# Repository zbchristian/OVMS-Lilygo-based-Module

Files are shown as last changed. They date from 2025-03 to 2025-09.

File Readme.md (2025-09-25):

Open-Vehicle-Monitoring-System: Module based on Lilygo T-Call A7670E V1.0/V1.1
==============================================================================
The Lilygo T-Call modules provide most of the hardware required for an OVMS module:
- ESP32-WROVER E with 4MB Flash and 8MB PSRAM
- Simcom A7670E 4G modem with GPS 
- Included antennas for 4G and GPS
- USB-C port for programming and powering during testing
- ext 5V powering possible via pin
- Price is around 35€ + tax

**This module supports only 2 CAN buses. This might limit the suitability for your car!**

OVMS Requirements
----------------- 
- Connection to OBD-II connector
- Powering via 12V of the OBD-II connector
- OBD-II to DSub-9 cable 

Communication with the car via CAN-bus requires
- Physical layer(s) and CAN controller
- 12V to 5V DC/DC converter and including filtering

Hardware
========
The Lilygo board is placed onto a motherboard, either into a socket, or the pins can be directly soldered to the board. The motherboard provides the voltage for the Lilygo board and the DSub-9 connector to connect to the OBD-II.
The board revision B is suitable for the T-Call version 1.0 and 1.1 (different GPIO mapping).

The image shows the module, the antennas and the 3D printed case (Freecad and Step files availybe in the `CAD` folder). The motherboard slides into slots and the lid will hold it in place.
The lid allows to store the GPS antenna, but allows to add SMA connectors for external antennas as well. The 4G antenna can be stored in a 1mm high compartment inside the case.

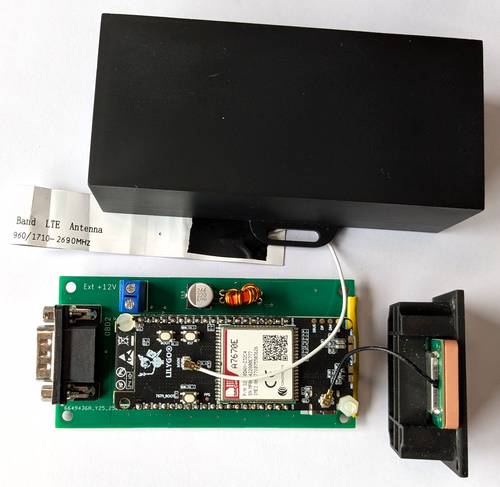
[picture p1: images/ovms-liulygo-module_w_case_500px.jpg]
OVMS module based on Lilygo T-Call


*The Lilygo based module and case. The GPS-antenna is placed into a corresponding slot in the lid of the case*

The chosen orientation (Simcom 7670 on the top) of the Lilygo board allows for easy access to the antenna connectors. The ESP32 WROVER E is in this case located on the bottom side.  

Features of the motherboard
---------------------------
The Lilygo T-Call is placed on a motherboard 
- size 49 x 98 mm²
- DSub-9 connector (pinout compatible standard OVMS module) to connect to the OBD-II
- 12V car battery input from the OBD-II, or a separate power souce 
- Fuse and filtering (common mode choke and capacitors) of the input voltage 
- DC/DC converter to provide the Lilygo board with 5V
    - Auto shutdown of the DC/DC converter at a voltage below 11.7V to prevent the drainage of the battery
    - A voltage of more than 11.9V is required to switch on again
- Two CAN busses are implemented
    - ESP32 internal requires only a physical layer
    - Second bus with an MCP2515 controller
    - Solder jumpers to enable 120 &Omega; bus termination resistors 
- Voltage divider to measure the battery voltage
- The schematic and board layout is provided for Autodesk Eagle
- The Gerber and bill of material is provided for the board production and assembly at JLCPCB 
- Nearly all components are placed on the bottom side of the PCB. This allows for an easy access, even when the Lilygo board is soldered to the motherboard
- 3D printable case to house the motherboard as well as the antennas
    - sufficient space in the lid to add SMA connectors for external antennas

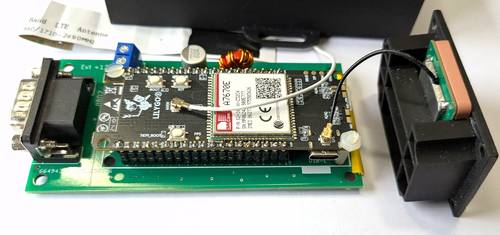
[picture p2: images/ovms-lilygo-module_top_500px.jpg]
OVMS module based on Lilygo T-Call - Top side

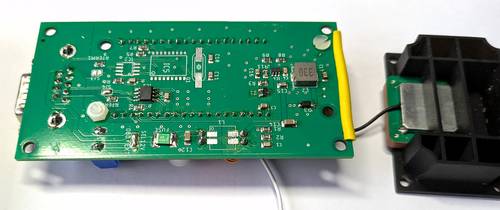
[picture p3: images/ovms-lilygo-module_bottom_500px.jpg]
OVMS module based on Lilygo T-Call - Bottom side


*Top and bottom side of the module. Only a single CAN bus is assembled, because the module is used for a car with a single bus. Therefore the second physical layer and the MCP2515 is left empty*

Limitations
-----------
- The flash memory size of only 4MB Flash does no allow Over-the-Air updates of the firmware. So, each change requires access via the USB-C port 
- Only two CAN buses
- No GPIO extender
- No SD-Card support

Assembly related hints
----------------------
The Lilygo module can in principle be soldered directly to the board by using the provided pin headers. The board has to be mounted with the Simcom modem on the top side.
Using a precision socket and corresponding pin headers, the module can easliy be removed again, but should be secured by non conducting screws.
 
The DC-DC converter output voltage is defined by R8 and R9. The reference voltage is 0.8V, so with R8=100k and R9=18k, the output voltage is about 5.2V.
The Schottky diode reduces this by about 0.4V, hence the Lilygo module is powered by 4.8V. The diode is necessary to allow to provide power via the USB-C 
port at the same time, i.e. when flashing a new firmware. 

The DC-DC converter exhibits an enable input, which requires a minimum voltage to power on of 1.2V and to power off of 1.0V. The enable voltage is derived from the 
input voltage by means of the Zener diode Z1 and the voltage divider R3/R11. For a Zener voltage of 10V, the default values R3=100k and R11=220k lead to 
a minimal power on voltage of 11.8V and a maximal power off voltage of 11.5V. In case a different Zener voltage is used, the divider has to be adjusted accordingly. 

Firmware
--------
Except for the above mentioned limitation, the module is compatible with the standard OVMS firmware, BUT the pinout requires a remapping of the ESP32 pins.
This is implemented in the [OVMS repository](https://github.com/openvehicles/Open-Vehicle-Monitoring-System-3). 
- Follow the standard OVMS documentation to clone the above repository, install the required additional packages and install the required Espressif IDF
- In the folder `./vehicle/OVMS.V3` copy `support/sdkconfig.lilygo_tc` to `sdkconfig` and `support/partition4M.csv` to `partition4M.csv`
- Run `make menuconfig` and go to `Component config -> Opene Vehicle Monitoring System (OVMS) -> Hardware support`.
  - Hardware Version should be 3.1
  - Enable GPIO remapping under `Choose GPIO Mapping`
  - Now a new menu entry appears in `Hardware support` called `File with GPIO mapping`
	- For the above `sdkconfig`, the default file is `lilygo_tc_v11.h`. This is valid for the Rev B motherboard and a Lilygo A7670E T-Call V1.1
	- The GPIO mappings files are located in the folder `components/gpio_maps`
- Be sure, that the following OVMS components are disabled: MAX7317, external SWCAN, Over-The-Air update, SD card
- Disable the support for all cars (`vehicle support`) except for the one you are interested in. This is required to meet the limited space in the Flash memory for the firmware
  - For the default `partitions4M.csv`, the available space for the firmware is `0x2f0000 = 3080192B = 2.94MB`. The full firmware requires about 3.5MB.
  - **The support for the *Nissan Leaf* and *Renault Twizzy* should always be disabled, since these do not compile without the MAX7317 support.**  
- Follow the standard documentation to compile and flash the firmware via USB
  - Check the size of the firmware: `ls -la build/ovms3.bin`
- If the flash process is failing due to a too large firmware
  - disable some additional cars under `Vehicle support`
  - if no corresponding scripts are utilized, disable the Javascript support (under `OVMS3 library suppoprt`). This saves about 220kB
  - disable components which are not needed, like the *ZIP archive support* (`OVMS3 library support`) and the `OVMS3 component options` *Reverse Engineering tools*, *ECU scanning*, *File editor*, *Plugins*
- The above limitation for the firmware size can be reduced, by using a modified partition table ([`partitions4M_full.csv`](partitions4M_full.csv)) from this repository
  - This reduces the `FAT` partition, the storage for the OVMS configuration, from `1MB` to `512kB`, which might cause problems in your setup!
  - In this case the available space for the firmware is `0x370000 = 3604480B = 3.44MB`

Alternative GPIO mapping
-------
Alternative GPIO mapping files are available and can be placed in the folder [`components/gpio_maps`](https://github.com/openvehicles/Open-Vehicle-Monitoring-System-3/tree/master/vehicle/OVMS.V3/components/gpio_maps). 

Check the [Readme](https://github.com/openvehicles/Open-Vehicle-Monitoring-System-3/tree/master/vehicle/OVMS.V3/components/gpio_maps) for details about the naming of the GPIO pins and the format of the mapping files.

Known Issues
------------
- An outdated firmware version of the Simcom A7670E can cause connection problems. The firmware can be updated according to the
[Modem Firmware Update Guide](https://github.com/Xinyuan-LilyGO/LilyGO-T-A76XX/blob/main/docs/update_fw.md). 
This requires to solder an USB cable to the corresponding pins on the Lilygo board (see [here](https://github.com/Xinyuan-LilyGO/LilyGO-T-A76XX/issues/180)).

Disclaimer
==========
This design is provided as is. Use at your own risk.

Enjoy!

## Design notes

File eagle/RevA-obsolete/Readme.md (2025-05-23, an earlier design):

Obsolete Revision A of the motherboard
======================================
The first version of the motherboard is only suitable for the Lilygo T-Call A7670E V1.0!

Due to re-arranged GPIOs is the board not compatible with T-Call V1.1.

The revision B board can be used for both T-Call versions, but requires a different GPIO mapping in the software.

Modification of a Rev A board into a Rev B: 
- Cut connection of GPIO 32 to the transceiver chip (CAN-TX) -> connect with GPIO 2
- Cut the conenction of GPIO 33 (CAN transceiver RS) -> conenct with GPIO 21

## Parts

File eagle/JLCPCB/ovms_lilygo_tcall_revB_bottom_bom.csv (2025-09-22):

Comment | Designator | Footprint | LCSC Part #
1u | C16 | C0805K
2u2 | C15 | C0805K
10K | R5 R6 R7 | M0805
10V | Z1 | SOT23
10k | R4 | M0805
18k | R9 | M0805
22pF | C10 C11 | C0805K
22u | C3 | C0805K
22u | C12 C14 | C1206K
22u | C17 | C0805K
33u | L2 | DR74
100k | R2 R3 R8 | M0805
100n | C1 C4 C6 C7 | C0805K
120 | RTERM0 RTERM1 | M0805
220k | R11 | M0805
470k | R1 | M0805
LMR51610XDBVR | IC4 | SOT23-6
MCP2515T-I/SO | IC5 | SO-18W
MF-SMDF050 | FUSE | MF-SMDF050
SS12 | D3 | SOD123
TCAN330DR | IC2 IC3 | SO-08
WE-SL2 250uH 1.2A | L1 | CHOKE_SMD
X49SM16MSD2SC | Q1 | 11.4X4.5

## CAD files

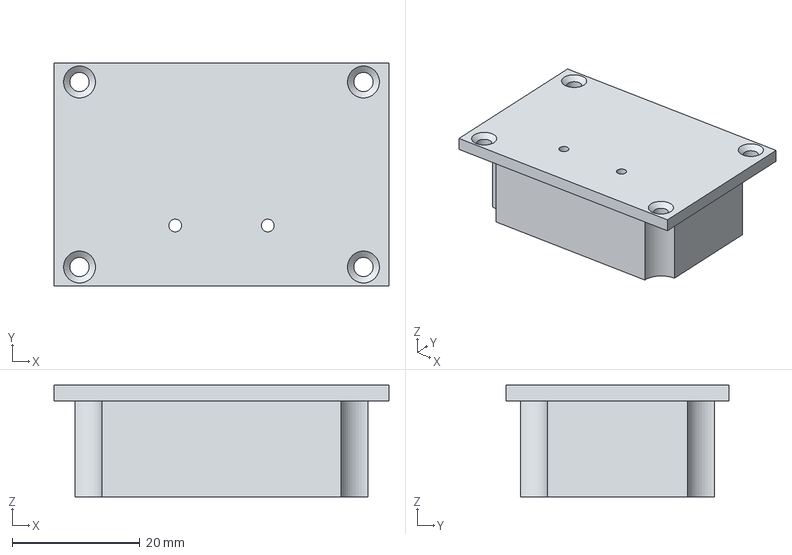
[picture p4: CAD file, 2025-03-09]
CAD/case-v2-lid.step
52.5 x 35.0 x 17.5 mm

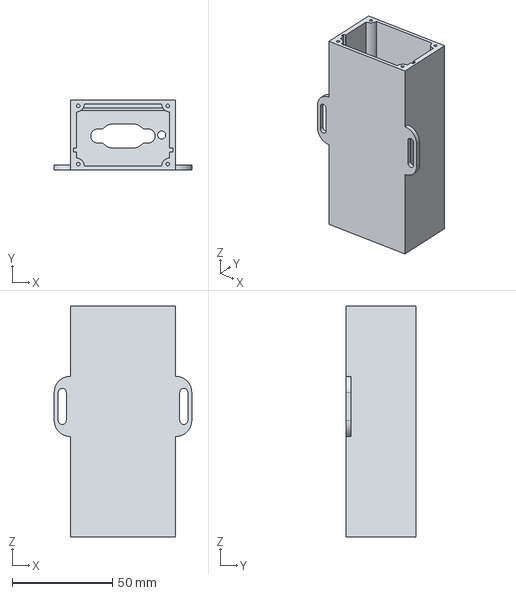
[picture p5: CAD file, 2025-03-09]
CAD/case_v2.step
68.5 x 35.0 x 115.0 mm

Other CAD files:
CAD/case-v2.FCStd

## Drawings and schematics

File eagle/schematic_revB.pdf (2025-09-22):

# GPIO22 LILYGO

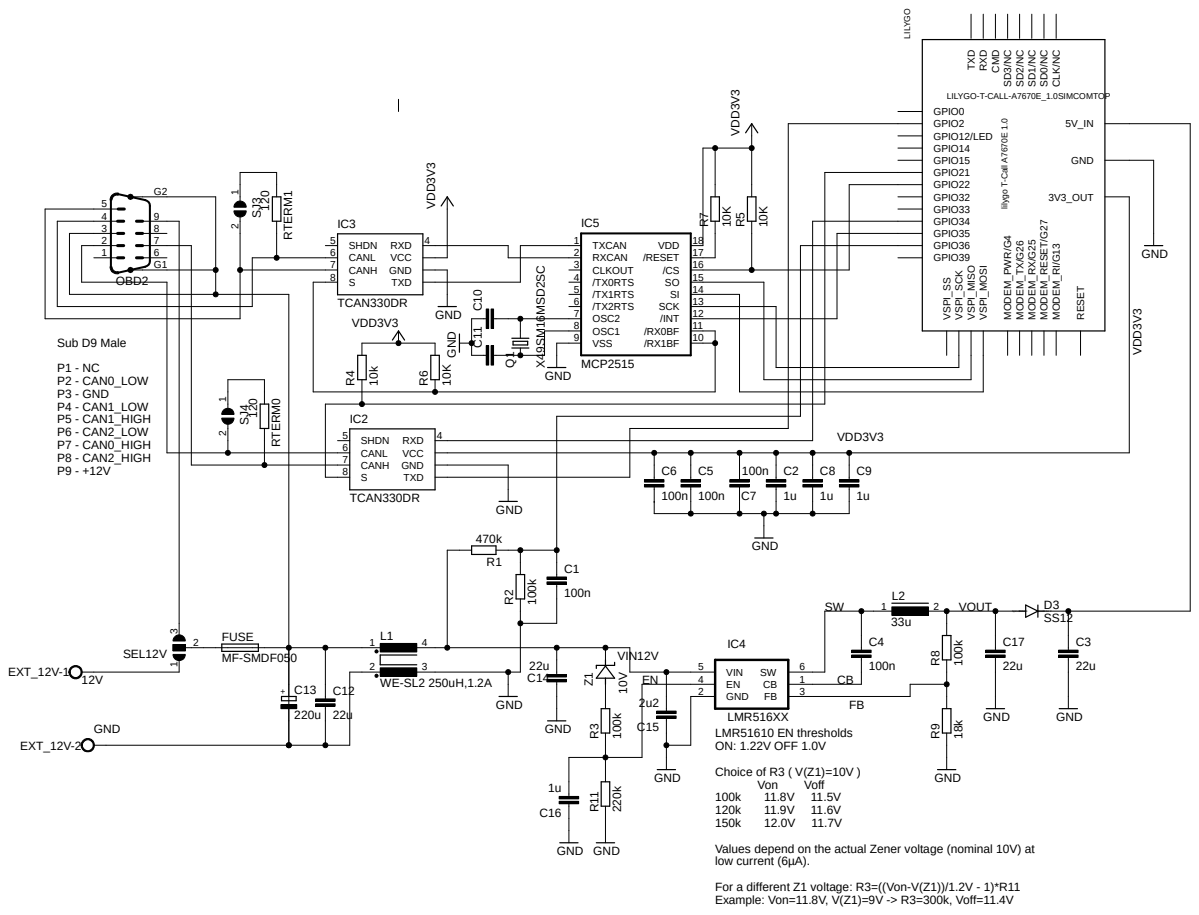
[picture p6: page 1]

3V3_OUT SD³/NC SD²/NC SD¹/NC SD⁰/NC CLK/NC TXD RXD CMD

LMR51610 EN thresholds
ON: 1.22V OFF 1.0V
Choice of R3 ( V(Z1)=10V )
Values depend on the actual Zener voltage (nominal 10V) at
low current (6µA).
For a different Z1 voltage: R3=((Von-V(Z1))/1.2V - 1)*R11
Example: Von=11.8V, V(Z1)=9V -> R3=300k, Voff=11.4V

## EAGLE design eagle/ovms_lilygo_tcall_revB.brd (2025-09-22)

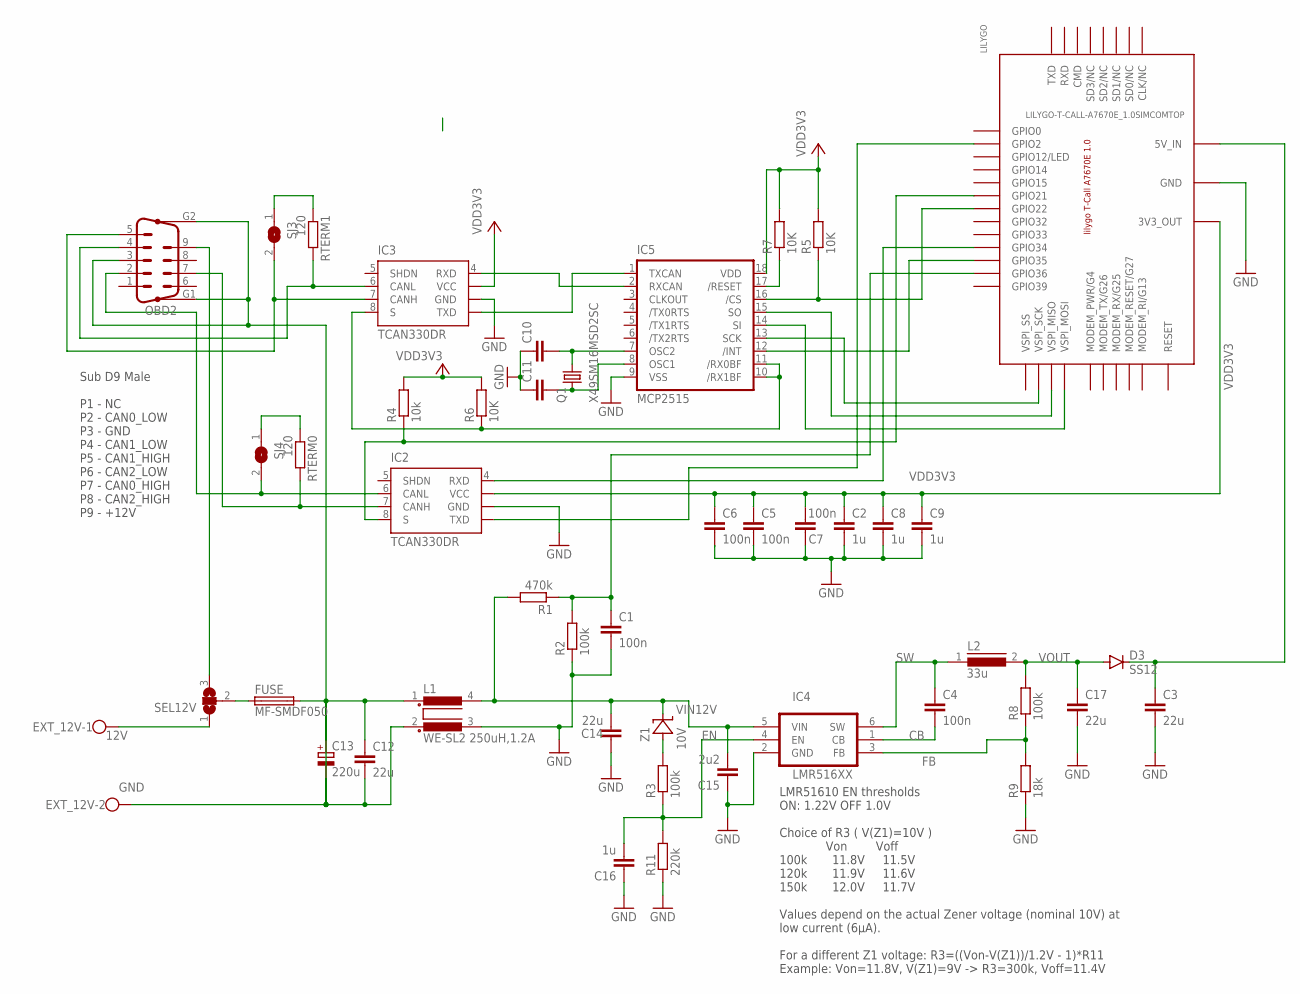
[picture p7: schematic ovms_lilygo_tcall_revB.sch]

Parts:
C1, C4, C5, C6, C7: 100n; C0805K
C2, C8, C9, C16: 1u; C0805K
C3, C17: 22u; C0805K
C10, C11: 22pF; C0805K
C12, C14: 22u; C1206K
C13: 220u; UD-8X10_NICHICON
C15: 2u2; C0805K
D3: SS12; SOD123
EXT_12V: GND; W237-102
FUSE: MF-SMDF050
IC2, IC3: TCAN330DR; SO-08
IC4: LMR516XX; SOT23-6
IC5: MCP2515; SO-18W
L1: WE-SL2 250uH,1.2A; CHOKE_SMD
L2: 33u; DR74
LILYGO: LILYGO-T-CALL-A7670E_1.0SIMCOMTOP; LILYGO-TCALL-A7670E_1.0
OBD2: M09HP
Q1: X49SM16MSD2SC; 11.4X4.5
R1: 470k; M0805
R2, R3, R8: 100k; M0805
R4: 10k; M0805
R5, R6, R7: 10K; M0805
R9: 18k; M0805
R11: 220k; M0805
RTERM0, RTERM1: 120; M0805
SEL12V: SJ2W; SJ_2
SJ3, SJ4: SJ
Z1: 10V; SOT23

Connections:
12V: C12.1, C13.+, FUSE.2, L1.1
CB: C4.2, IC4.1 (CB)
EN: C16.2, IC4.4 (EN), R3.1, R11.2
EXT12V: EXT_12V.1, SEL12V.1
FB: IC4.3 (FB), R8.1, R9.2
GND: C1.2, C2.2, C3.2, C5.2, C6.2, C7.1, C8.2, C9.2, C10.1, C11.1, C14.1, C15.1, C16.1, C17.2, IC2.2 (GND), IC3.2 (GND), IC4.2 (GND), IC5.9 (VSS), L1.3, LILYGO.1 (GND), LILYGO.7 (GND), LILYGO.25 (GND), R2.1, R9.1, R11.1
GND1: C12.2, C13.-, EXT_12V.2, L1.2, OBD2.3, OBD2.G1, OBD2.G2
unnamed: IC3.1 (TXD), IC5.1 (TXCAN)
unnamed: FUSE.1, SEL12V.2
unnamed: IC3.4 (RXD), IC5.2 (RXCAN)
unnamed: IC5.17 (/RESET), R7.1
unnamed: IC5.16 (/CS), LILYGO.3 (GPIO22), R5.1
unnamed: IC3.8 (S), IC5.10 (/RX1BF), IC5.11 (/RX0BF), R6.1
unnamed: C10.2, IC5.7 (OSC2), Q1.2
unnamed: R3.2, Z1.1 (A)
unnamed: IC2.4 (RXD), LILYGO.34 (GPIO34)
unnamed: IC2.1 (TXD), LILYGO.15 (GPIO2)
unnamed: IC2.6 (CANL), OBD2.2, SJ4.2
unnamed: IC2.8 (S), LILYGO.6 (GPIO21), R4.1
unnamed: IC2.7 (CANH), OBD2.7, RTERM0.2
unnamed: IC3.6 (CANL), OBD2.4, RTERM1.2
unnamed: IC3.7 (CANH), OBD2.5, SJ3.2
unnamed: C1.1, LILYGO.36 (GPIO36), R1.1, R2.2
unnamed: IC5.12 (/INT), LILYGO.33 (GPIO35)
unnamed: C11.2, IC5.8 (OSC1), Q1.1
unnamed: IC5.13 (SCK), LILYGO.9 (VSPI_SCK)
unnamed: IC5.15 (SO), LILYGO.8 (VSPI_MISO)
unnamed: IC5.14 (SI), LILYGO.2 (VSPI_MOSI)
unnamed: RTERM1.1, SJ3.1
unnamed: RTERM0.1, SJ4.1
OBD12V: OBD2.9, SEL12V.3
SW: C4.1, IC4.6 (SW), L2.1
VCC5V: C3.1, D3.C, LILYGO.20 (5V_IN)
VDD3V3: C2.1, C5.1, C6.1, C7.2, C8.1, C9.1, IC2.3 (VCC), IC3.3 (VCC), IC5.18 (VDD), LILYGO.38 (3V3_OUT), R4.2, R5.2, R6.2, R7.2
VIN12V: C14.2, C15.2, IC4.5 (VIN), L1.4, R1.2, Z1.3 (C)
VOUT: C17.1, D3.A, L2.2, R8.2

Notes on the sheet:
Sub D9 Male P1 - NC P2 - CAN0_LOW P3 - GND P4 - CAN1_LOW P5 - CAN1_HIGH P6 - CAN2_LOW P7 - CAN0_HIGH P8 - CAN2_HIGH P9 - +12V
LMR51610 EN thresholds ON: 1.22V OFF 1.0V Choice of R3 ( V(Z1)=10V ) Von Voff 100k 11.8V 11.5V 120k 11.9V 11.6V 150k 12.0V 11.7V Values depend on the actual Zener voltage (nominal 10V) at low current (6µA). For a different Z1 voltage: R3=((Von-V(Z1))/1.2V - 1)*R11 Example: Von=11.8V, V(Z1)=9V -> R3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

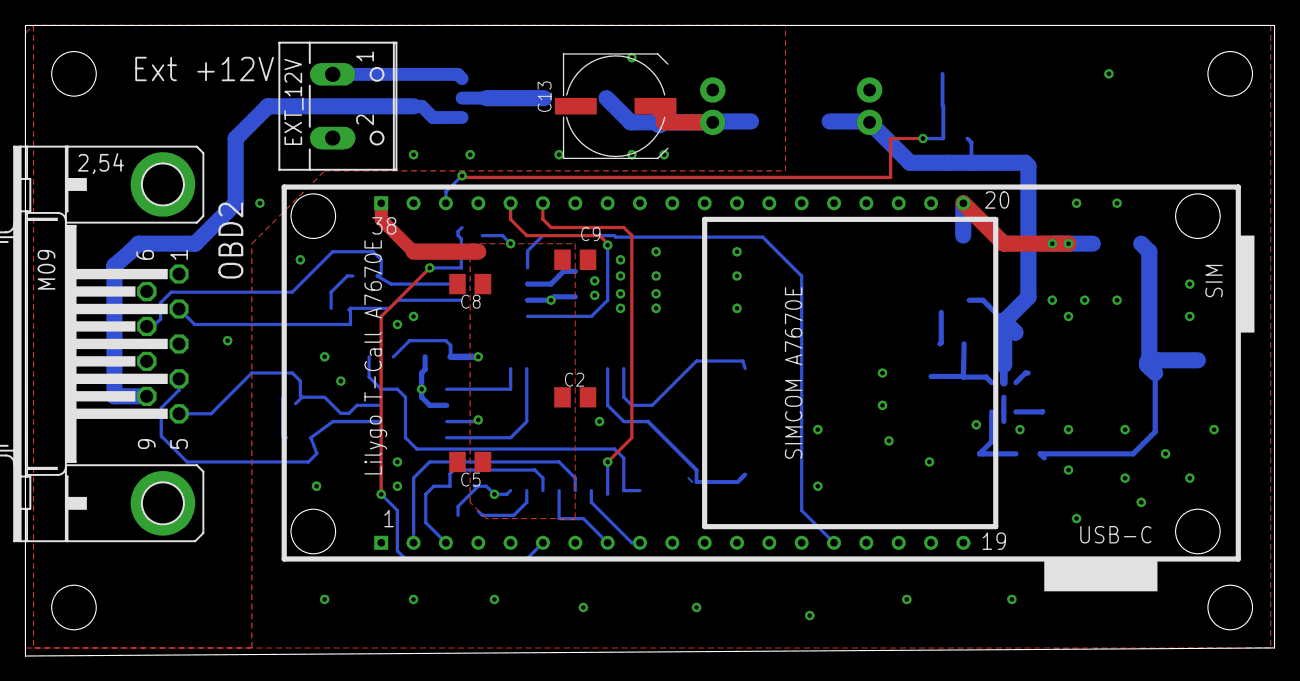
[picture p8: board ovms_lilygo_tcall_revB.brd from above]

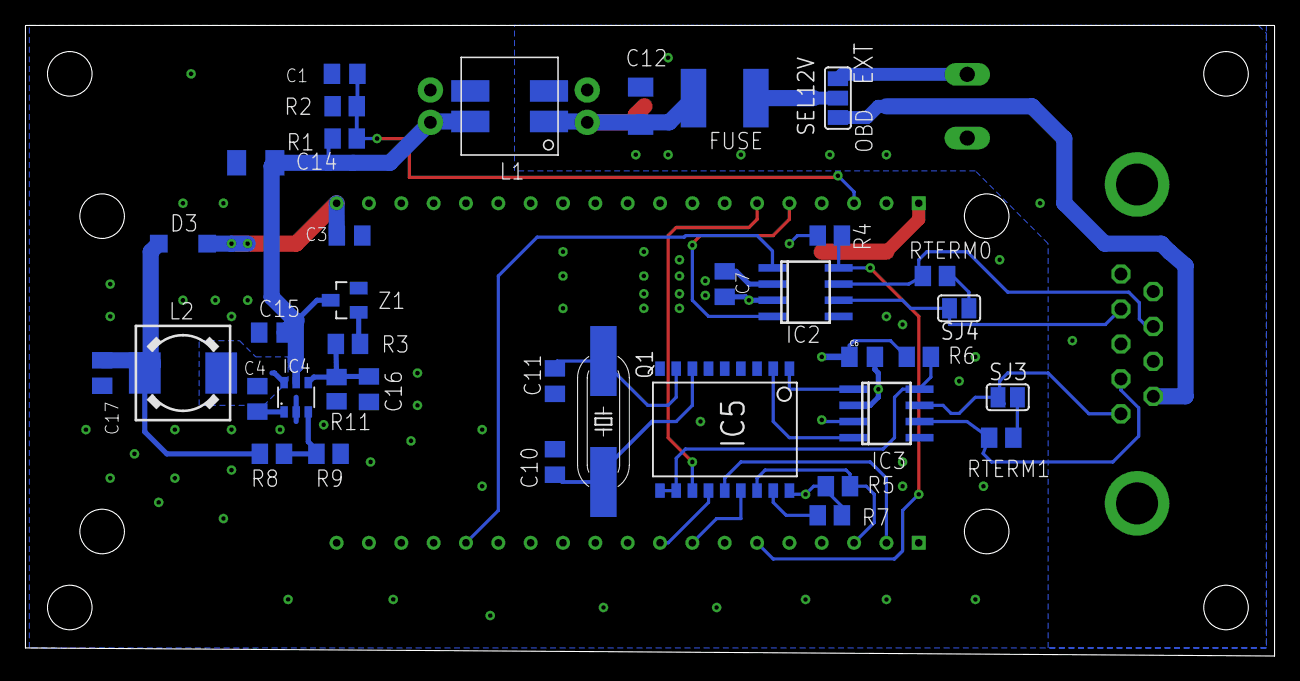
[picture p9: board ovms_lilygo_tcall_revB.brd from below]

Board: 2 copper layers, 98.1 x 49.5 mm, 45 parts (37 on the bottom side), 36 nets.

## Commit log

2025-02-21 Motherboard and case for Lilygo-T-Call A7670E as OMS
    [case-v2-lid.step, case-v2.FCStd, case_lid_v1.stp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]
2025-03-09 Correct width an hole position of case
    [case-v2-lid.step, case-v2.FCStd, case_v2.step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]
2025-04-26 Clean up Eagle
    [ovms_lilygo_tcall.brd, ovms_lilygo_tcall.sch, ovms_lilygo_tcall_pic.sch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]
2025-04-26 Remove old case files
    [case_lid_v1.stp, case_v1.FCStd, case_v1.stp]
2025-04-29 Adjust resistors for low current (DCDC off)
    [ovms_lilygo_tcall.brd, ovms_lilygo_tcall.sch, ovms_lilygo_tcall_v_1_0_bottom_bom.csv]
2025-05-16 Rename first version files to RevA and add RevB eagle files
    [ovms_lilygo_tcall_revA.brd, ovms_lilygo_tcall_revA.sch, ovms_lilygo_tcall_revA_bottom_bom.csv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]
2025-05-19 Update motherboard to Rev B to support T-Call 1.0 and 1.1
    [ovms_lilygo_tcall_revA.brd, ovms_lilygo_tcall_revA.sch, ovms_lilygo_tcall_revA_bottom_bom.csv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]
2025-05-23 Undelete Rev B eagle files
    [ovms_lilygo_tcall_revB.brd, ovms_lilygo_tcall_revB.sch]
2025-05-23 Change schematic to increase default DCDC output voltage
    [ovms_lilygo_tcall_revB.brd, ovms_lilygo_tcall_revB.sch, ovms_lilygo_tcall_revB_bottom_bom.csv]
2025-06-11 Replace CAN transceiver (TCAN330)
    [ovms_lilygo_tcall_revB.brd, ovms_lilygo_tcall_revB.sch, ovms_lilygo_tcall_revB_bottom_bom.csv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]
2025-09-22 Update documentation wrt modified OVMS repository
    [partitions4M_full.csv]

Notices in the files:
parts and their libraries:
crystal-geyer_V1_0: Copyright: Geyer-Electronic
